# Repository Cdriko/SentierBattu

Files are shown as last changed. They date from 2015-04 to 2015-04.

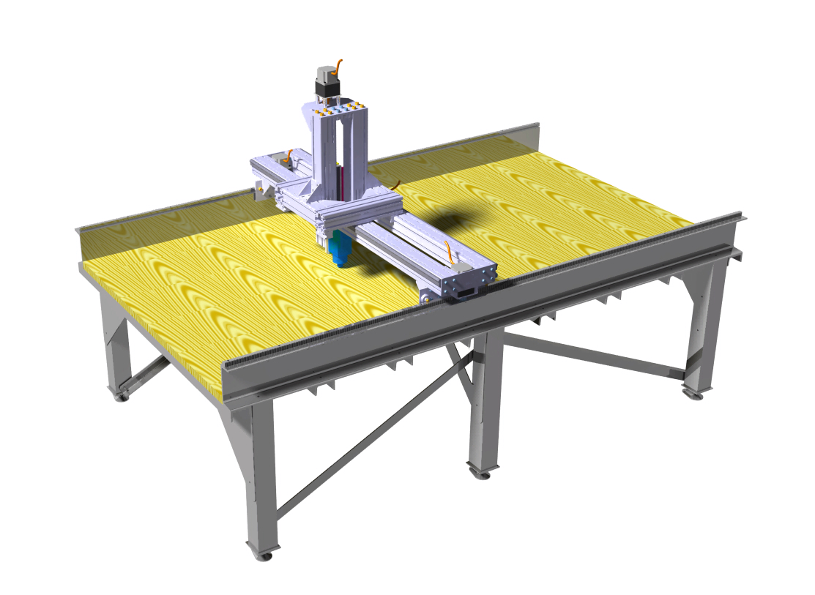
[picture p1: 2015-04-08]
sentierBattu.projet.jpg

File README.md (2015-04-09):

# SentierBattu
large CNC opensource router

Created by association PiNG 
http://pingbase.net

License : creative comons CC-BY-SA

Cedric Doutriaux

Laurent Malys

Philippe Bonet

Eric Chotard

Laurent Berthelot

with the help of

IUT of Nantes

more infos on
http://fablabo.net/wiki/SentierBattu

#######

For piloting it use fabmodules
https://github.com/FabModules/fabmodules-html5

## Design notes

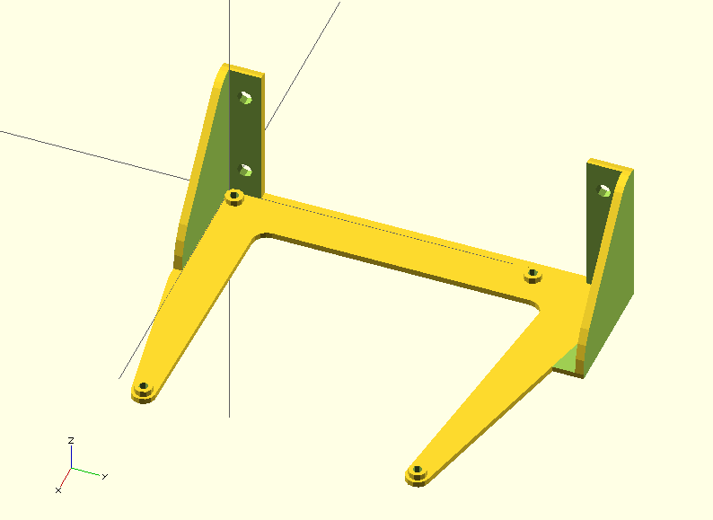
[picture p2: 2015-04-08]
electrics/electronics/smoothieBox/smoothifixation.png

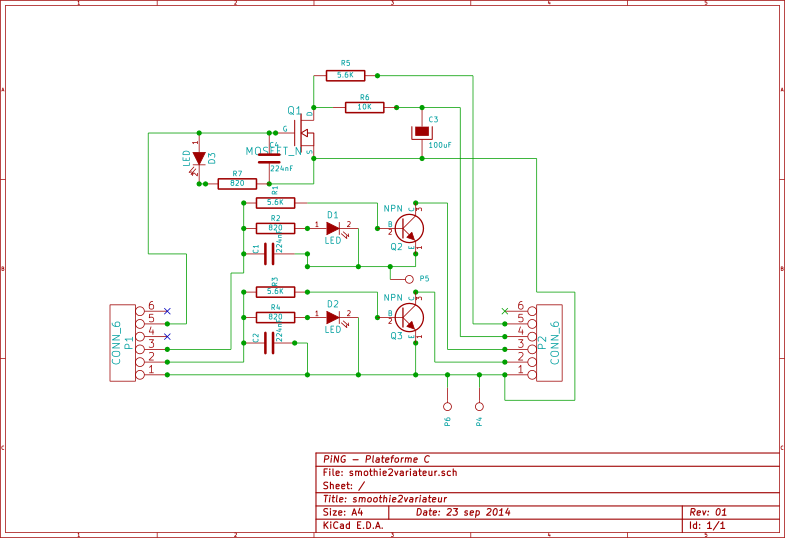
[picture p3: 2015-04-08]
electrics/electronics/Smothie2variateur.png

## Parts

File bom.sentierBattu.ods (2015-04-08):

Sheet: Résumé
Budget Machine CNC
electronique | 3792,45
mécanique | 5541,34312
Budget total machine | 9333,79312
Budget prévu | 9100

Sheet: electronique
electronique
 |  | qtte | fournisseur | modele | ref | option PP
controleur moteur |  | 3 | http://www.geckodrive.com/geckodrive-step-motor-drives/g201x.html |  |  | 120 | 360
moteur |  | 4 | http://www.orientalmotor.fr/Products/Stepper_motors/Stepper_motors/2phase_motors_pk/?arid=4646 | Motoreducteur nema34 | PK296AE-SG7.2 | 253,5 | 1014
Transformateur 220/24 |  | 1 |  |  |  | 170 | 170
 |  |  |  |  |  |  | 0
 |  | 1 |  |  |  | 0 | 0
moteur meche |  | 1 | www.fimec.it | 1.5KW 18/24000 RPM HF SPINDLE MOTOR | HM73d-060 | 585 | 707,85
controleur meche |  | 1 | www.fimec.it | INVERTER MONOFASE 220V | DSR2M022 | 360 | 435,6
 |  |  |  |  |  |  | 0
Armoire+rails |  | 1 |  |  |  | 120 | 120
cosses marqueurs |  | 1 |  |  |  | 50 | 50
Boutons |  | 5 |  |  |  | 5 | 25
arret d'urgence |  | 3 |  |  |  | 30 | 90
marche (poussoir) |  | 1 |  |  |  | 30 | 30
contacteur |  | 1 |  |  |  | 100 | 100
fins de course (logique + et -) |  | 6 |  |  |  | 40 | 240
ordinateur |  | 1 |  |  |  | 150 | 150
Cables / relais |  | 1 |  |  |  | 300 | 300
pour circuit electrique
disjoncteur diferentiel 30mA 20A | Q1 |  | rs | Disjoncteur iID 2pôles 25A 30mA c.a. | 510-6478
disjoncteur magnéto thermique D 4A | Q2 |  | rs |  | 772-1240
disjoncteur D 10A | Q3 |  |  |  | 769-4738
Disjoncteur courbe C 25A | Q4 |  |  |  | 769-4615
Contacteur bobine 24Vcc + 3 poles NO | K1 |  |  |  | 394-9762
deux contacts BLOC CONT 2F FRONTAL | K1 |  |  |  | 394-9914
Filtre RFI MX2 200Vca 24A jusqu'à 2,2kW pour variateur | RFI |  |  |  | 705-1787
arrets d'urgence | AU1-2-3 | 3 |  |  | 330-8559
bouton poussoir démarrage | BP1 |  |  |  | 690-6884
pince à sertir |  |  |  |  | 247-391
blindage pour cables
cable de commande
marqueurs pour cables
Armoire+rails
 |  |  |  |  |  | TOTAL | 3792,45

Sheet: mécanique
Mécanique |  |  |  |  |  |  | fournisseurs
 | usage |  |  |  |  |  | FIO | HPC | AMD | radiospares
table
UPN 200X75X6m | rails longitudinaux | 6 | m |  |  | AMD Ouest chailloux (nantes) |  |  | 181,792
UPN 100X50X18m | structure transversale | 18 | m |  |  |  |  |  | 203,32
Profilé carré creux 100X100 4mm | pieds | 6 | m |  |  |  |  |  | 83,72
profilé en L 50X50 4mm | Contre-ventement | 6 | m |  |  |  |  |  | 47,84
plaque 4mm 2X1m | équerres | 2 | m² |  |  |  |  |  | 143,52
pieds réglabes | pieds | 6 | u |  | 300Kg gros patin |  | 62,28
guidages
scheaffler 3mX2 | guidage X | 6 | m |  | peut être moins cher en morceaux de 1m chez rs |  |  | 1100,32
chariots X4 | X | 4 | u | hepco W3X |  |  |  |  |  | 225,51776
douilles de guidage |  |  |  |  |  |  |  |  |  | X
 |  |  |  |  |  |  |  |  |  | X
clinquant (feuilles de callage) 1/10 & 5/100 | réglage surface guidages X
guidages bosh LF12S | Z | 0,5 | m |  | rail double | FIO st herblain (sautron) | 52,31
guidages bosh LF12C | Y | 1,75 | m |  | de rail double | aller sur place
charriots LF12 | Y Z | 8 | u |  | + lardons |  | 699,12
entraînements
Crémaillères 4X2 module 2 | X | 6 | m |  | Dents droites percées acier | HPC distributeur |  | 297,99536
Pignons module 2 | X et Y | 4 | u |  | ~ d 30mm |  |  |  |  | X
crémaillère bosh module 2 | Y | 1,75 | m
vis a bille (500mm) diametre 16 pas~ 5mm | Z | 1 | u |  |  |  |  | 93,39564
ecrou pour vis a bille |  | 1 | u |  |  |  |  | 221,88192
palier fixe pour vis à bille |  | 1 | u |  |  |  |  | 302,5282
profilé 'bosh' 90X90mmn 4 trous | Chassis Y Z | 6 | m |  |  |  | 395,08
equerres bosh |  | 20 | u |  |  |  | 285,4
lardons bosh / equerres + guidages +charriots |  | 50 | u |  |  |  | 37
 |  |  |  |  |  |  |  |  |  |  | 0
 |  |  |  |  |  |  | 2289,32 | 2016,12112 | 660,192 | 575,71
 |  |  |  |  |  |  | 5541,34312

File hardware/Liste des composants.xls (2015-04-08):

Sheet: Feuil1
Quantité | Référence
3 | sg_2020-2000x
2 | poutrelle_upn_200_x_1_75
2 | rail
2 | 3842992415_104211921
2 | BOUCHON
20 | Vis chc m12 x 40
20 | Rondell m12
4 | Galet guidage axe x
8 | Ecrou_M12
4 | l1-16101
4 | Axe roulement
4 | Rondelle d'appui D19
4 | Vis M8 x 12
2 | TOLE GUIDAGE
4 | Equerre 90x90xx
40 | Vis_M8x25
56 | rondelle_9
101 | Ecrou BOSCH M8
74 | Lardon tige BOSCH-M8X25
2 | Tole moteur
4 | PK296AE-SG7.2
8 | Vis_M6x20
8 | rondelle_6-6
24 | vis_M8x16
3 | Pignon_moteur
2 | Profile de serrage LF12C x 750
2 | Tige de guidage LF12 x 750
8 | vis_M8x30
4 | plaque support fin de course
4 | Fin_de_course_DL
8 | vis_07175-04x25
8 | ecrou_M4
1 | UPN 200x75x3000
8 | UPN 100x50x1750
1 | UPN 200x75x3000.1
1 | Plaque martyr
4 | equerre.1
2 | equerre
6 | PLAT PIED
18 | ecrou_3300-408
6 | tige filetée M12
6 | bosch_3842538680_38kq0hejlxcjebzu4812w7e6w
6 | Tube carré 100x100x820
6 | Part8
8 | vis_m10_20
2 | contreventement long
2 | contreventement court
2 | sg_20-20-3000
2 | railx3000
36 | ISO 7089 WASHER 12x24 STEEL GRADE A PLAIN NORMAL SERIES
5 | Butée axe X
1 | Planche bois
2 | Profil 90*90 X
2 | profil 90*90 Y
8 | chariot Y
8 | Equerre 90*90
1 | IPN
2 | Plaque_machine_chariot_Y
2 | vis_07175-06x12
20 | ISO 4762 SCREW M12x30 STEEL HEXAGON SOCKET HEAD CAP
2 | 500
1 | 3842992415_102757468
1 | Profile de guidage LF12S
1 | 3842993062_10302278
2 | 3842993968_103214500
1 | 3842990335_103324390
1 | 3842992415_104211921_2
1 | Plaque broche
1 | broche
1 | Part2
1 | Ecrou_GBS-F-1605
4 | tube
4 | ISO 10642 SCREW M6x10 STEEL HEXAGON SOCKET COUNTERSUNK HEAD
2 | ISO 10642 SCREW M6x30 STEEL HEXAGON SOCKET COUNTERSUNK HEAD
2 | ISO 4762 SCREW M8x40 STEEL HEXAGON SOCKET HEAD CAP
2 | lardon_M8
6 | ISO 4032 NUT M5 STEEL GRADE A HEXAGON
6 | ISO 10642 SCREW M5x25 STEEL HEXAGON SOCKET COUNTERSUNK HEAD
2 | lardon M6
1 | accouplement
1 | Vis_KGS-1605-1000TR7
1 | Part1
2 | cale 6mm
1 | Palier_RPB12
1 | Support_palier
4 | Entretoise_moteur
1 | Rehausse_moteur
1 | tranche profilé 90x90x20
1 | Part3
4 | ISO 4762 SCREW M5x35 STEEL HEXAGON SOCKET HEAD CAP
8 | ISO 4762 SCREW M8x30 STEEL HEXAGON SOCKET HEAD CAP
1 | boitier_electrique
3 | Boutan_arret_urgence
1 | AL-AL001-1 1/2in

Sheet: Feuil2
Quantité | Référence |  | commentaire
3 | sg_2020-2000x | ok
2 | poutrelle_upn_200_x_1_75
2 | rail
2 | 3842992415_104211921
2 | BOUCHON | ok
4 | l1-16101
4 | Axe roulement | ok
2 | TOLE GUIDAGE | ok
4 | Equerre 90x90xx
2 | Tole moteur | ok
4 | PK296AE-SG7.2
8 | rondelle_6-6
3 | Pignon_moteur
2 | Profile de serrage LF12C x 750
2 | Tige de guidage LF12 x 750
4 | plaque support fin de course | ok | poutre z -9
4 | Fin_de_course_DL
1 | UPN 200x75x3000
8 | UPN 100x50x1750
1 | UPN 200x75x3000.1
1 | Plaque martyr
4 | equerre.1
2 | equerre
6 | PLAT PIED
18 | ecrou_3300-408
6 | bosch_3842538680_38kq0hejlxcjebzu4812w7e6w
6 | Tube carré 100x100x820
6 | Part8
2 | contreventement long
2 | contreventement court
2 | sg_20-20-3000
2 | railx3000 | ok | ( rail guidage x )
36 | ISO 7089 WASHER 12x24 STEEL GRADE A PLAIN NORMAL SERIES
5 | Butée axe X
1 | Planche bois
2 | Profil 90*90 X
2 | profil 90*90 Y
8 | chariot Y
8 | Equerre 90*90
1 | IPN | ok
2 | Plaque_machine_chariot_Y
1 | 3842992415_102757468
1 | Profile de guidage LF12S
1 | 3842993062_10302278
2 | 3842993968_103214500
1 | 3842990335_103324390
1 | 3842992415_104211921_2
1 | Plaque broche
1 | broche
1 | Part2
4 | tube
1 | Part1
2 | cale 6mm
1 | Palier_RPB12
1 | Support_palier
4 | Entretoise_moteur | ok
1 | Rehausse_moteur | ok
1 | tranche profilé 90x90x20
1 | Part3
1 | AL-AL001-1 1/2in
 | Plans fais mon pas de correspondance en nomenclature ????
 | poutre z 1 | ok
 | poutre z 2 | ok
 | poutre z 4 | ok
 | vis kgs | ok
 | poutre z 6 | ok
 | poutre z 7 | ok
 | profilés | ok
 |  | ok
 |  | ok
 |  | ok
 |  | ok
 |  | ok

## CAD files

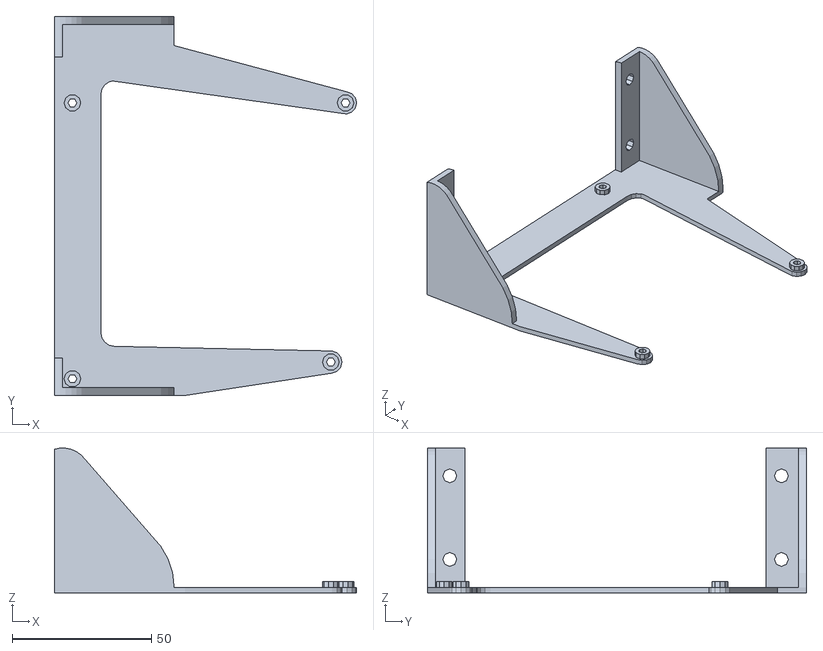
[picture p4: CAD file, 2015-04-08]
electrics/electronics/smoothieBox/SmootieBox.stl
108.5 x 136.0 x 51.9

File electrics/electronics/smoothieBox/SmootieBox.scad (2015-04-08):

/*
Smoothieboard attach for electrical enclosure
*/



module smoothieholes(){
translate([0,0,-4])
union(){//holes
		
			translate([3.5,3,-30])
			cylinder(r=1.6,h=60);
			
			translate([3.5,102,-30])
			cylinder(r=1.6,h=60);
			
			translate([(105-8.77),9,-30])
			cylinder(r=1.6,h=60);
			translate([(105-3.5),102,-30])
			cylinder(r=1.6,h=60);
		
		}


}



module SmoothiePlate(){
	//-------------------smoothieBoard
	difference(){
translate([0,0,-0.75])
		cube([105,130,1.5]);
		translate([0,0,-1])
		smoothieholes();
	}
//USB port
translate([77,0,-0.75])
		cube([12.3,16.6,10.8]);
}

//background rail
module backSupport(){
	//back support
translate([0,0,-0.5])
linear_extrude(height = 1,center=true){
union(){
	hull() {
	   translate([3.5,3,0])
				circle(12);
	   translate([(105-8.77),9,0]) circle(4);
	}
	hull() {
	translate([(105-3.5),102,0])circle(4);
	 translate([3.5,122,0])
				circle(10);
	translate([3.5,127,0])
				circle(4);
	 }
	difference(){
		hull() {
		translate([(3.5),102,0])circle(17.2);
		 translate([(3.5),9,0]) circle(15);
		 }
		hull() {
		translate([(18.7),105,0])circle(5);
		 translate([(18.7),19.6,0]) circle(5);
		 }
	}
}
}

union(){//holes
		
			translate([3.5,3,0])
			cylinder(r=3,h=1);
			
			translate([3.5,102,0])
			cylinder(r=3,h=1);
			
			translate([(105-8.77),9,0])
			cylinder(r=3,h=1);
			translate([(105-3.5),102,0])
			cylinder(r=3,h=1);
		
		}



}



module arch(){//for the wall fixation

	difference(){
	
		//Arch
		rotate([90,0,0])
		linear_extrude(height = 15,center=true)
		hull() {
				translate([22,0,0])circle(25);
				 translate([7,40,0]) circle(10);
				 }
		union(){//wall holes

rotate([0,-90,0]){
			translate([10,2,-40])
			cylinder(r=2.5,h=60);
			translate([40,2,-40])
			cylinder(r=2.5,h=60);
}

		}
		
	
	}
}


difference(){





	union(){

difference(){
translate([-7,0,0])
union(){
		//archs
		translate([0,3,0])
		arch();




		translate([0,126,0])
mirror([0,1,0])
		arch();
}

union(){
translate([0,-0.2,0])
cube([105,130.4,500]);

}
}
		
		
		//total backplate
		difference(){
		scale([1,1,2])
		backSupport();
		
		}
	}

	union(){//bounding box
	
		translate([-10,133,-20])
		cube([105,130,300]);
		translate([-10,-33,-20])
		cube([105,30,300]);
		
		translate([-3,137.5,-20])
		rotate([0,0,180])
		cube([105,160,300]);
		
		translate([-20,-25,-32])
		cube([305,300,30]);
smoothieholes();
	
	}

}
///smoothie preview
//color([0.9,0.4,0.2,0.5])
//SmoothiePlate();

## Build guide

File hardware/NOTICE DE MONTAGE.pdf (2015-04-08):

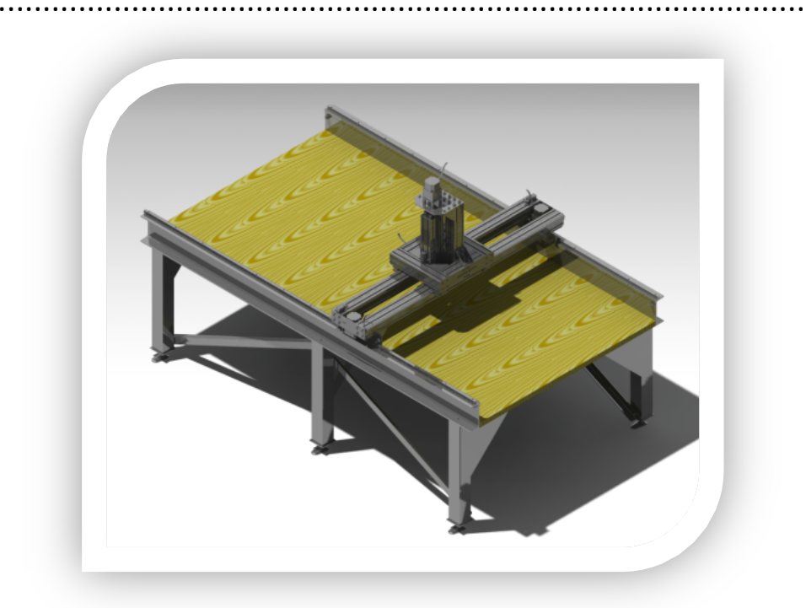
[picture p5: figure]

FAB

LAB

– Workshop

CNC

Router 1

# NOTICE

DE

# MONTAGE :

SOMMAIRE :

Description

des

sous

Montage

du

Assemblage

des

traverses

Mise

en

place

des

pieds

et

des

positionnement

des

Retournement

du

Montage

du

chariot

Assemblage

de

la

structure

axe

Assemblage

des

deux

ensembles

de

Assemblage

des

deux

parties

Montage

de

Montage

du

chariot

Matériels

Montage

du

chariot

AXE

Z

Structure

AXE

DESCRIPTION

DES

SOUS ENSEMBLES :

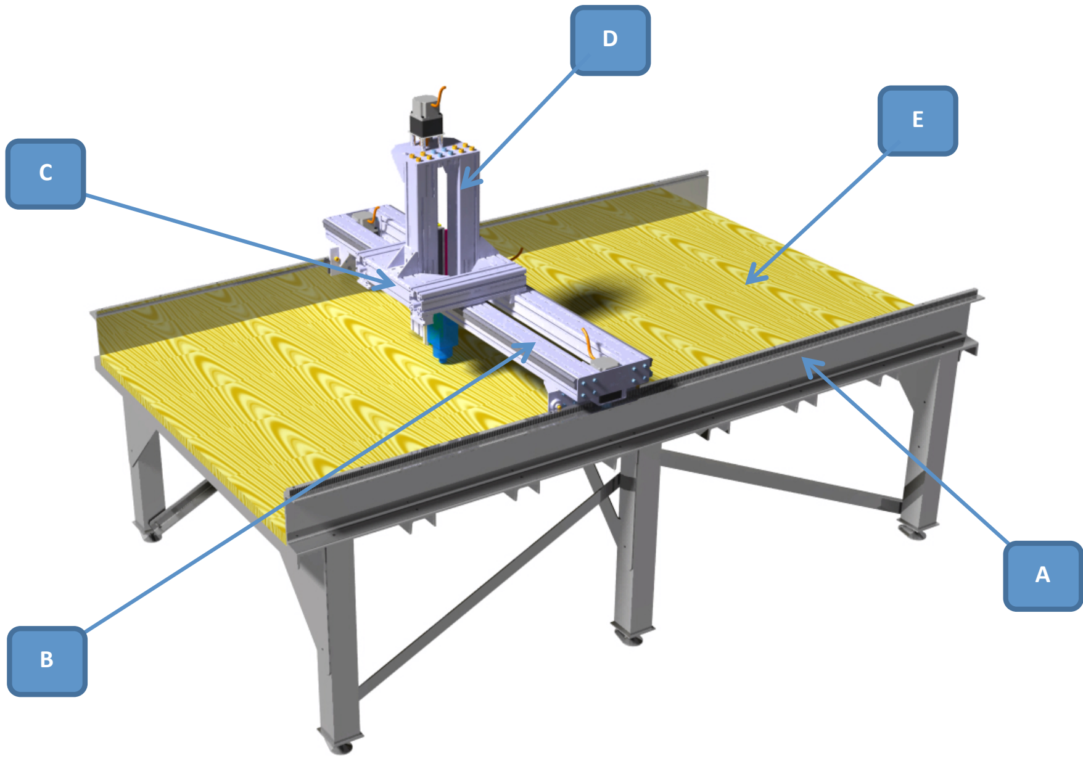
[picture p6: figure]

### A. La

### machine

### est

### composée

### d’un

bâti,

### sur

### lequel

### sont

### fixées

### les

### crémaillères

de

### l’axe

x

### ainsi

### que

### les

### deux

### rails

de

guidage.

### B. Le

### chariot

X

### est

### guidé

### sur

### les

### deux

### rails

### par

### des

galets,

la

### transmission

de

### mouvement est

### assurée

### par

### deux

### moteurs

### électriques

### montés

en

### vis

à

vis.

### C. Le

### chariot

Y

### est

### guidé

### sur

le

### chariot

de

### l’axe

X,

la

### transmission

### est

### assurée

### par

un

### moteur

### électrique

### engrenée

### sur

### une

crémaillère.

### D. L’axe

Z

### est

### porté

### par

le

### chariot

Y,

### cet

### axe

### porte

la

broche.

La

### transmission

### est

### assurée par

### une

### vis à

bille.

### E. Le

### plateau

### support

### autrement

### appelé

### plaque

### martyr

### est

### réalisé

en

### contreplaqué

de
40

mm.

MONTAGE

DU

BATI :

ASSEMBLAGE

DES

TRAVERSES

(UPN) :

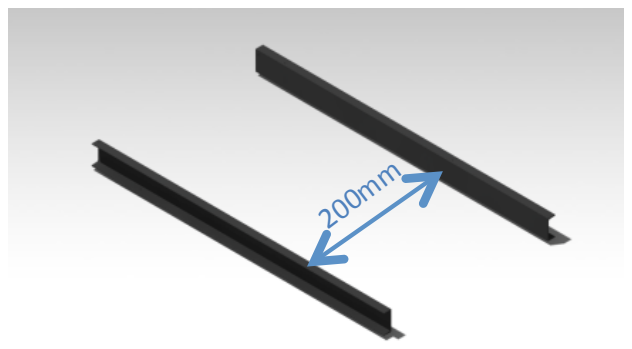
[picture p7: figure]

- Dans

un

premier

temps,

positionner

les

deux

grosses

traverses
(UPN

200x75x3000) au

sol

sur

des

cales,

dégauchir

l’ensemble.
Puis,

positionner

et

dégauchir

les

traverses

extrêmes

après

avoir
serré

légèrement.

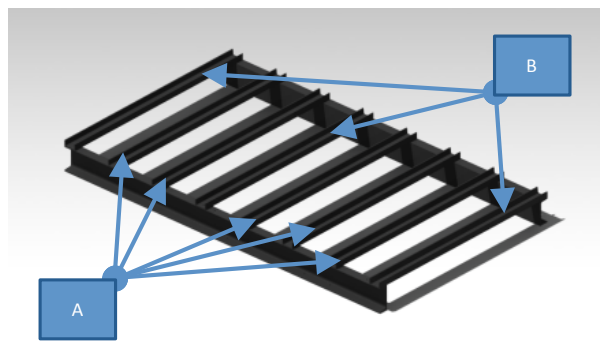
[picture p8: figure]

- Pour

le

déchauchissage,

utiliser

des

équerres,

un

mètre

afin

de
mesurer

la

largeur

et

les

diagonales.

- Positionner

et serrer

les

autres

traverses (UPN

100x50x1750). Il

y

a
deux

types

de

traverses.

Trois

d’entre

elles

(Type

B)

possèdent

des
perçages

sur

les

flancs

de

l’UPN

pour

la

fixation

des

goussets

de
pieds.

MISE

EN

PLACE

DES

PIEDS

ET

DES

GOUSSETS :

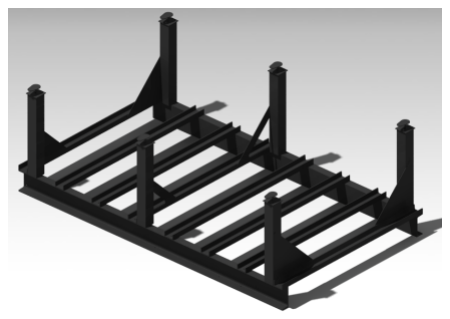
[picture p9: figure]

- Visser

les

pieds

dans

la

structure

sans

les

serrer à

l’aide

des

vis
M12,

positionner

les

goussets et

les

serrer

après

avoir

contrôler
les

équerrages

et

les

cotes

,

attention

,

les

deux

goussets

centraux
sont

différents

de

ceux

des

extrémités.

POSITIONNEMENT

DES

CONTREVENTEMENTS :

- Dans

cette

étape,

il

va

falloir

souder

les

têtes

de

vis

(En

rouge)

sur
la

face

intérieure

des

pieds.

Au

préalable,

il

faut

visser

les

vis

sur

le
contreventement

en

ayant

pris

soin

de

mettre

un

contre

écrou
coté

tête

de

vis

afin

de

dégager

celle-‐ci

pour

le

pointage.

RETOURNEMENT

DU

CHASSIS :

- Pour

retourner

le

châssis,

positionner

deux

sangles

autour

d’un

des

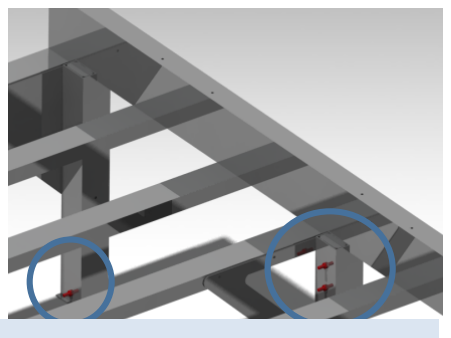
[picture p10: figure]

UPN

de

200

mm,

positionner

deux
tasseaux

qui

supporteront

l’UPN

opposé

lors

de

la

phase

de

rotation.
- Une

fois

l’ensemble

retourné,

lever

l’ensemble

à

la

verticale

à

une

vingtaine

de

centimètre

pour
pouvoir

monté

les

pieds

réglables

à

rotule.

On

peut

ensuite

repositionner

la machine

dans

sa

position
définitive

de

montage.
- Il

faut

ensuite

dégauchir l’ensemble,

à

l’aide

d’un

laser,

de

règles

ou

de

niveaux

de

précision.

La
largeur

des

deux

UPN

de

200

mm

doit

également

être

réglée,

prise

de

côtes

et

de

diagonales.

MONTAGE

DU

CHARIOT

X :

ASSEMBLAGE

DE

LA

STRUCTURE

AXE

X :

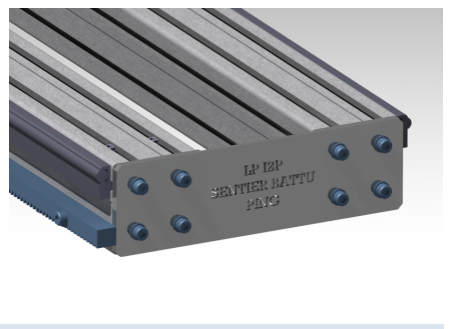
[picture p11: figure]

- Positionner

les

deux

profilés

de

90x90

et

fixer,

de

chaque

côté,

la
tôle

de

4mm

à

l’aide

des

8

vis

M12.

Il

faut

que

l’écart

entre

les
deux

profilés

soit

de

120mm

en

cote

intérieure.
- On

peut

ensuite

positionner

les

deux

rails

de

guidage

Bosch

sur

les
profilés

en

les

clipsant

dans

les

rainures.

Vissage

de

la

crémaillère
à

l’aide

de

lardons

de

profilés.

ASSEMBLAGE

DES

DEUX

ENSEMBLES

DE

GUIDAGE :

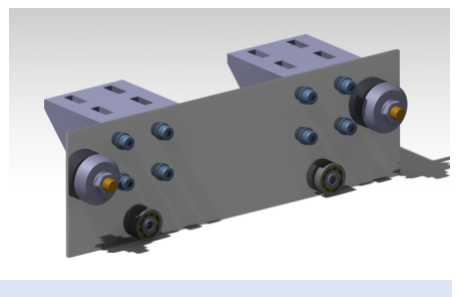
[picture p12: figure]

- Fixer

les

deux

équerres

Bosch

sur

la

tôle

support
- Positionner

les

deux

galets

et

les

deux

roulements

ASSEMBLAGE

DES

DEUX

PARTIES

MOTEURS :

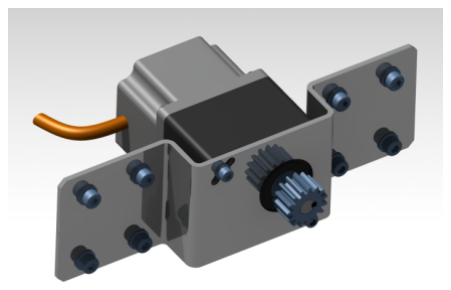
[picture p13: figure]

- Positionner

le

moteur

dans

son

logement

et

le

fixer

à

l’aide

des
deux

vis.
- Monter

le

pignon

sur

l’arbre

moteur

à

l’aide

de

la

clavette

et

le
maintenir

en

position

avec

la

vis

sans

tête

qui

appuie

sur

le
méplat

de

l’arbre.

MONTAGE

DE

L’ENSEMBLE :

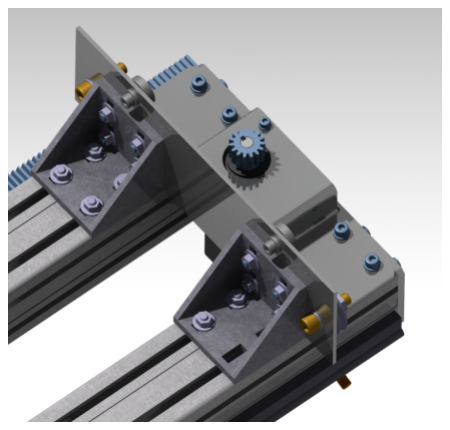
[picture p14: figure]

- Fixer

les

deux

ensembles

de

guidage

avec

les

écrous

et

lardons
pour

profilés.
- Fixer

les

deux

parties

moteurs

à

l’aide

des

8

vis.

MONTAGE

DU

CHARIOT

Y :

MATERIELS

NECESSAIRES :

Afin

de

réaliser

le

montage

du

chariot

vous

aurez
besoin

de :

-‐ 2 profilés

Bosch

de

90*90

de

450mm

de
| long
-‐ | 2 profilés

Bosch

de

90*90

de

310mm

de
| long
-‐ | 4 équerres

Bosch

de

90*90
-‐ 4 chariots

de

guidage

linéaire

LF12C
-‐ 34

lardons

males

M8

Bosch
-‐ 34

écrous

à

embase

M8
-‐ 10

lardons

femelles

M8

Bosch
-‐ 1 équerre

poutre

I

usinée
-‐ 2 vis

FHC

M8*12

-‐ 4 vis

CHC

M6*10
-‐ 4 rondelles

M6
-‐ 1 crémaillère

(Z=15)
-‐ 1 moteur

PK296AE
-‐ 2 plaques

gravées
-‐ 16

vis

CHC

M12

Et

du | matériel

suivant :

-‐ | 1 serre-‐joint
-‐ | 1 clef

à

pipe

et

une

clé

plate

de

13

pour
| les

écrous

à

embase
-‐ 1 clef

Allen

de

5

pour

les

CHC
-‐ 1 clef

Allen

de

…

pour

les

FHC

MONTAGE :

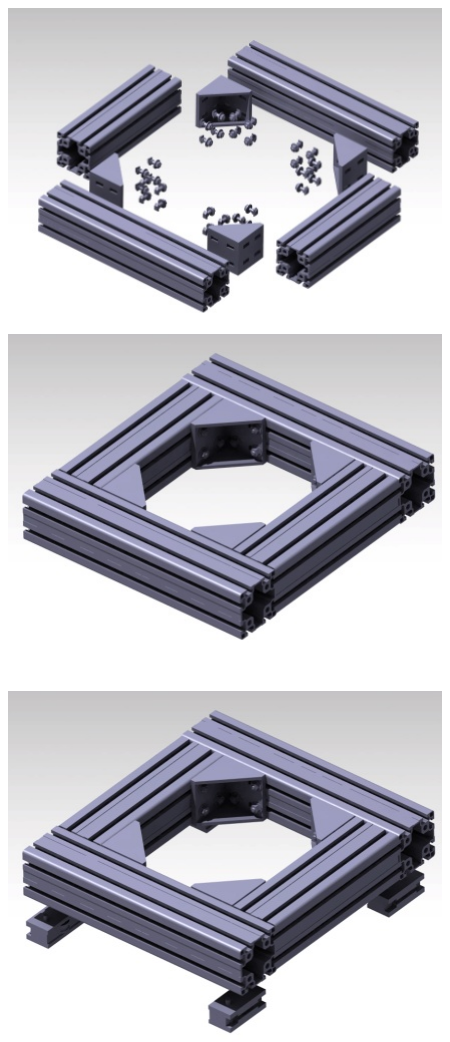
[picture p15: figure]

- Dans

un

premier

temps

vous

assemblerez

les

4

profilés

ensembles
à

l’aide

des

4

équerres

comme

ci-‐dessous

avec

32

des

lardons
males

et

32

des

écrous

à

embase

en

serrant

à

la

main

afin

de
permettre

le

glissement

des

différents

profilés
- Afin

de

réaliser

le

bon

écart

entre

les

deux

profilés

de

310

vous
aurez

besoin

de

3

profilés

de

90*90

de

petite

longueur

afin

de

les
utiliser

comme

cales

que

vous

serrerez

entre

les

profilés

pour
ensuite

serrer

les

32

écrous.
- Vous

placerez

ensuite

les

4

chariots

de

guidage

sur

les

profilés

de
450mm

de

long

à

l’aide

des

8

lardons

femelles

que

l’on

serra

à

la
main

si

possible

puis

à

la

clef

Allen

sans

forcer

afin

de laisser

la
possibilité

de

positionné

les

guidages

sur

les

rails

du

chariot

X.
- Il

faudra

ensuite

placer

le

chariot

Y

sur

le

chariot

X

afin

de

régler
les

guidages

et

de

préparer

la

poutre

en

I

et

le

moteur.
- Comme

cité

précédemment

vous

réglerez

les

guidages

à

l’aide

des
excentriques

sur

les

deux

rails

du

chariot

Y.
- Ensuite

vous

placerez

le

moteur

sur

l’équerre

avec

un
positionnement

médian

par

rapport

aux

trous

oblong

que

vous
serrerez

à

l’aide

de

2

vis

M6

et

2

rondelles.

- Après

ce

premier

réglage

placé

l’équerre

sur

le

bord

du

chariot

Y
placé

sur

le

chariot

X

du

côté

de

la

crémaillère

et

estimez

le

jeu
qu’il

y

a

entre

le

pignon

et

la

crémaillère

et

la

poutre

afin

de
rapprocher

ou

d’éloigner

le

moteur

ou

de

le

rapprocher

de

la
crémaillère.
- Recommencez donc

cette

étape

autant

de

fois

qu’il

sera

nécessaire
et

une

fois

que

l’équerre

sera

à

plat

et

le

pignon

bien

placé,

vous
pourrez

ajouter

les

deux

autres

vis

afin

de

fixer

le

moteur

sur

l’équerre.
- Retirez

le

chariot

Y

du

chariot

X

afin

de

pouvoir

fixer

l’équerre

sur
le

chariot

Y.
- Fixé

l’équerre

sur

la

poutre

à

l’aide

des

2

vis

FHC

et

des

lardons
femelles

du

côté

intérieur

et

les

2

lardons

males

et

écrous

à
embase

restants,

essayez

de

placer

l’équerre

entre

les

deux
chariots

de

guidage

afin

de

placer

la

motorisation

le

plus

au

centre

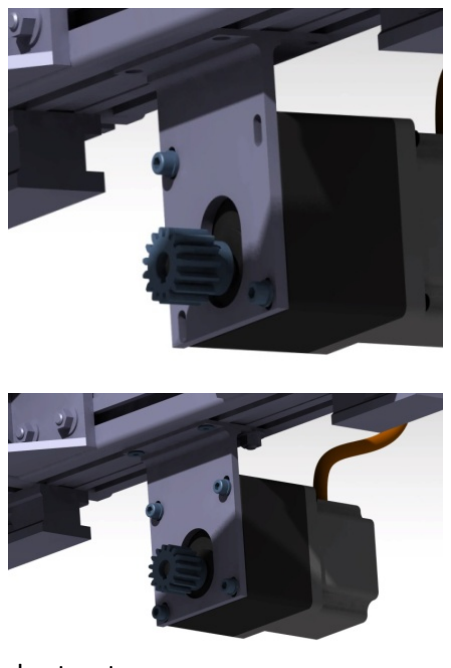
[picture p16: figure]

de

la

structure.
- Vous

placerez

enfin

les

deux

plaques

gravés

à

l’aide

des

16

vis

CHC

sur

les

extrémités

des

profilés
taraudé.

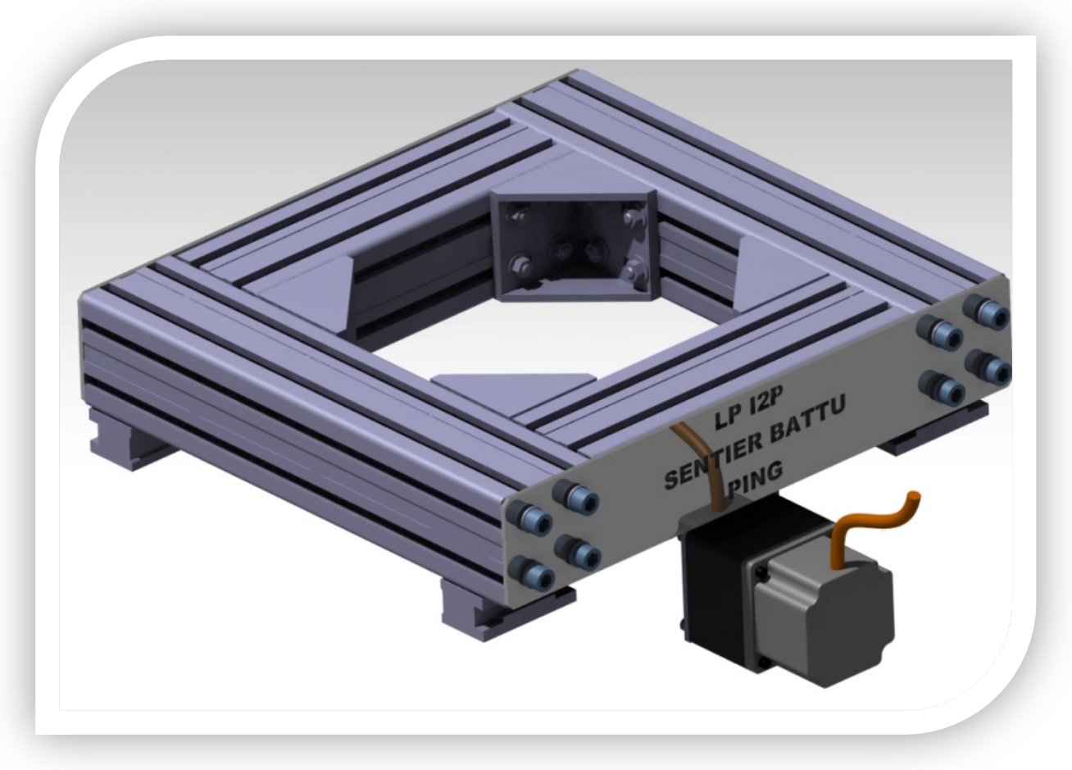
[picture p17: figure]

MONTAGE

DU

CHARIOT

Z :

AXE

Z

MOBILE :

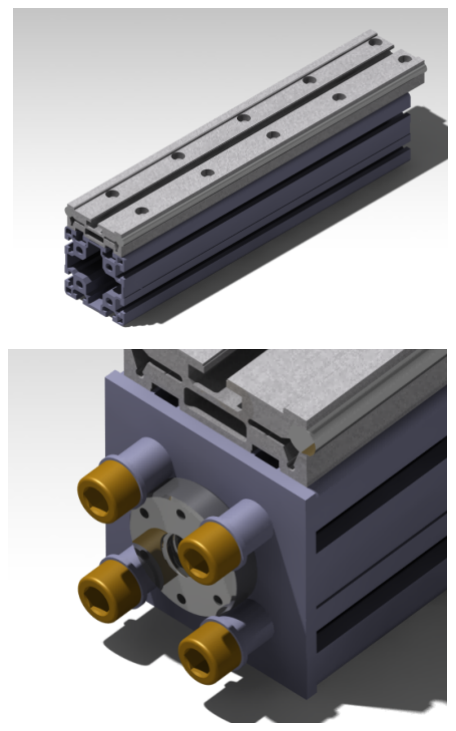
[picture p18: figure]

- Montage

du

profilé

de

guidage

sur

le

profilé

Bosch

de

90x90

et
mise

en

place

des

deux

axes

de

guidage

fournit

avec

le

profilé

de
guidage.
- Mise

en

place

de

l’écrou

de

vis

à

billes

sur

sa

plaque

en

acier

de
4mm

avec

6

vis

FHC

M5x25

et

6

écrou

H

M5.

- Mise

en

place

des

4

vis

M12

pour

fixer

la

plaque

support

de
l’écrou

sur

le

profilé.

Quatre

entretoises

ou

tubes

sont
nécessaires

car

les

têtes

de

vis

CHC

entraient

en

collision

avec
l’écrou

de

vis

à

billes.

- Mettre

les

deux

vis

FHC

M8

situé

sur

le

bas

de

la

plaque

puis

fixer
la

broche

sur

la

plaque

de

4mm

qui

permet

de

maintenir

la
broche

sur

le

guidage

Bosch.

On

utilise

4

vis

FHC

M6x12max.

On
visse

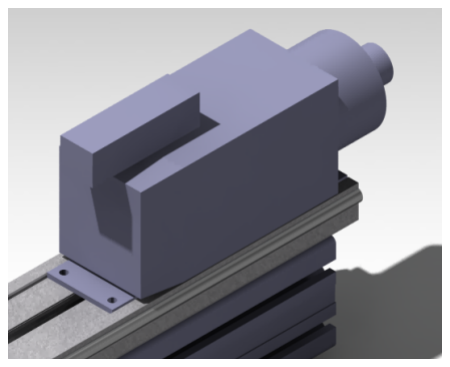
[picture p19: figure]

ensuite

les

deux

vis

inférieures

qui

ont

été

positionné

au
préalable

puis

les

deux

vis

CHC

M8.

Cette

plaque

est

fixée

à

l’aide
des

4

passages

de

vis

du

profilé

de

guidage

Bosch.

- Enfin

on

peut

positionner

le

capteur

de

fin

de

course

sur

le

profilé
Bosch

de

90x90.

La

hauteur

du

capteur

est

à

régler

et

à

définir
selon

l’épaisseur

de

la

plaque

martyre.

•

STRUCTURE

AXE

Z :

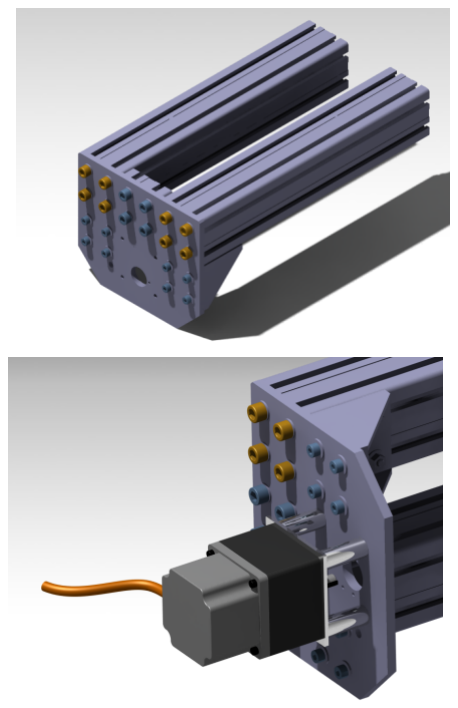
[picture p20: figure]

- Mettre

en

place

les

deux

profilés

de

500mm.

(Entraxe

intérieur
de

90mm.

- Positionner

la

tranche

de

profilé

de

90x90

qui

permet

d’assurer
l’entraxe

entre

les

deux

profilés. Cet

entraxe

est

important
puisque

la

broche

va

translater

entre

les

deux

profilés

Bosch.

- Positionner

la

plaque

aluminium

et

la visser

à

l’aide

des

8

vis
M12

sur

les

extrémités

des

deux

profilés.

- Visser

les

deux

équerres

à

l’aide

des

8

lardons

et

des

8

vis

M8

qui
permettront

de

renforcer

la

structure

Z.

Lors

du

montage

de

ces
équerres

il

faut

assurer

la

perpendicularité

de

la

plaque
aluminium

avec

les

deux

profilés

90x90

de

500mm.

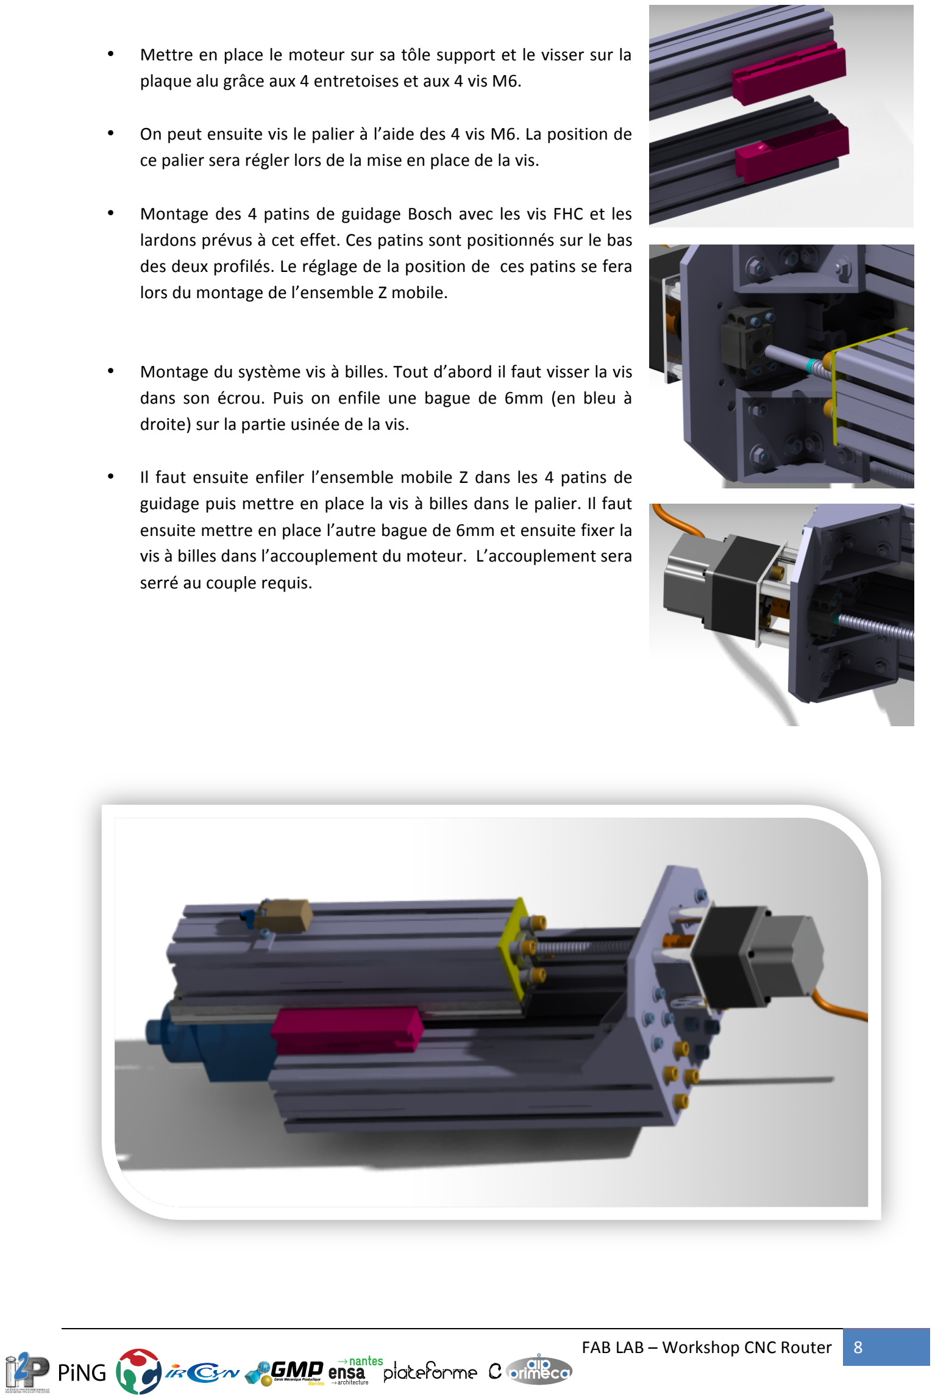
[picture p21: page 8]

- Mettre

en

place

le

moteur

sur

sa

tôle

support

et

le

visser

sur

la
plaque

alu

grâce

aux

4

entretoises

et

aux

4

vis

M6.

- On

peut

ensuite

vis

le

palier

à

l’aide

des

4

vis

M6.

La

position

de
ce

palier

sera régler

lors

de

la

mise

en

place

de

la

vis.

- Montage

des

4

patins

de

guidage

Bosch avec

les

vis

FHC

et

les
lardons

prévus

à

cet

effet.

Ces

patins

sont

positionnés

sur

le

bas
des

deux

profilés.

Le

réglage

de

la

position

de

ces

patins

se

fera
lors

du

montage

de

l’ensemble

Z

mobile.

- Montage

du

système

vis

à

billes.

Tout

d’abord

il

faut

visser

la

vis
dans

son

écrou.

Puis

on

enfile

une

bague

de

6mm

(en

bleu

à
droite)

sur

la

partie

usinée

de

la

vis.

- Il

faut

ensuite

enfiler

l’ensemble

mobile

Z

dans

les

4

patins

de
guidage

puis

mettre

en

place

la

vis

à

billes

dans

le

palier.

Il

faut
ensuite

mettre

en

place

l’autre

bague

de

6mm

et

ensuite

fixer

la
vis

à

billes

dans

l’accouplement

du

moteur.

L’accouplement

sera
serré

au

couple

requis.

ASSEMBLAGE

DES

DIFFERENTES

PARTIES :

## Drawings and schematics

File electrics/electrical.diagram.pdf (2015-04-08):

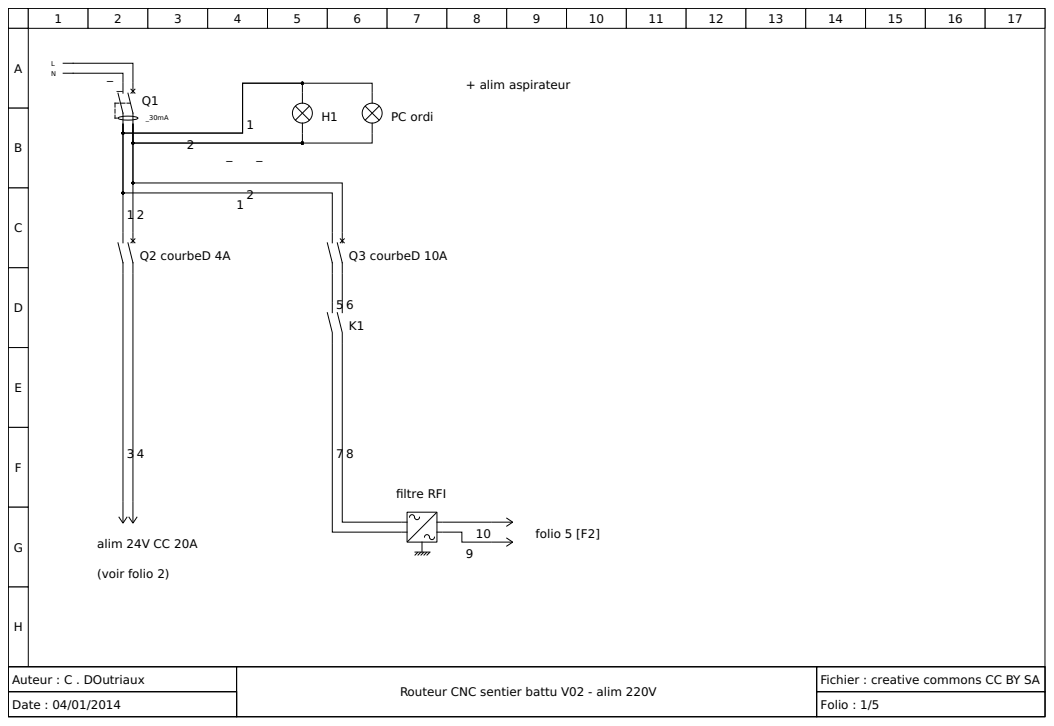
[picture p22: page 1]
Auteur : C . DOutriaux; Date : 04/01/2014; Folio : 1/5; PC ordi; Q2 courbeD 4A; Q3 courbeD 10A; + alim aspirateur; alim 24V CC 20A; (voir folio 2); filtre RFI; folio 5 [F2]

Fichier : creative commons CC BY SA

Routeur CNC sentier battu V02 - alim 220V

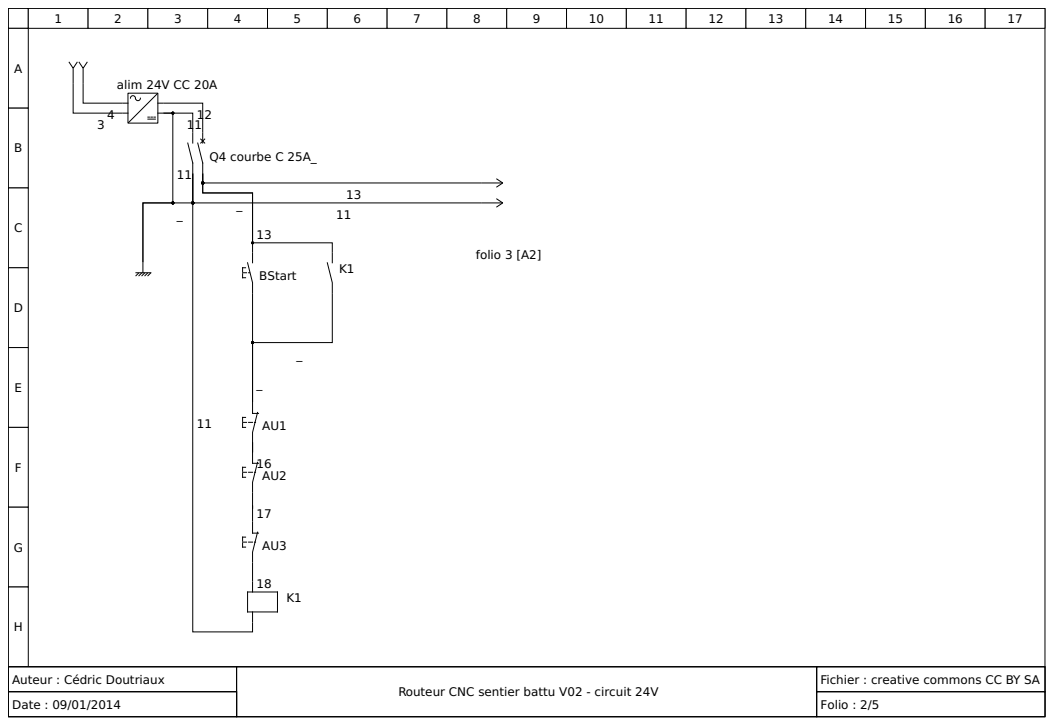
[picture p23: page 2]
Date : 09/01/2014; Folio : 2/5; Q4 courbe C 25A_; K1 BStart; alim 24V CC 20A; folio 3 [A2]

Auteur : Cédric Doutriaux

Fichier : creative commons CC BY SA

Routeur CNC sentier battu V02 - circuit 24V

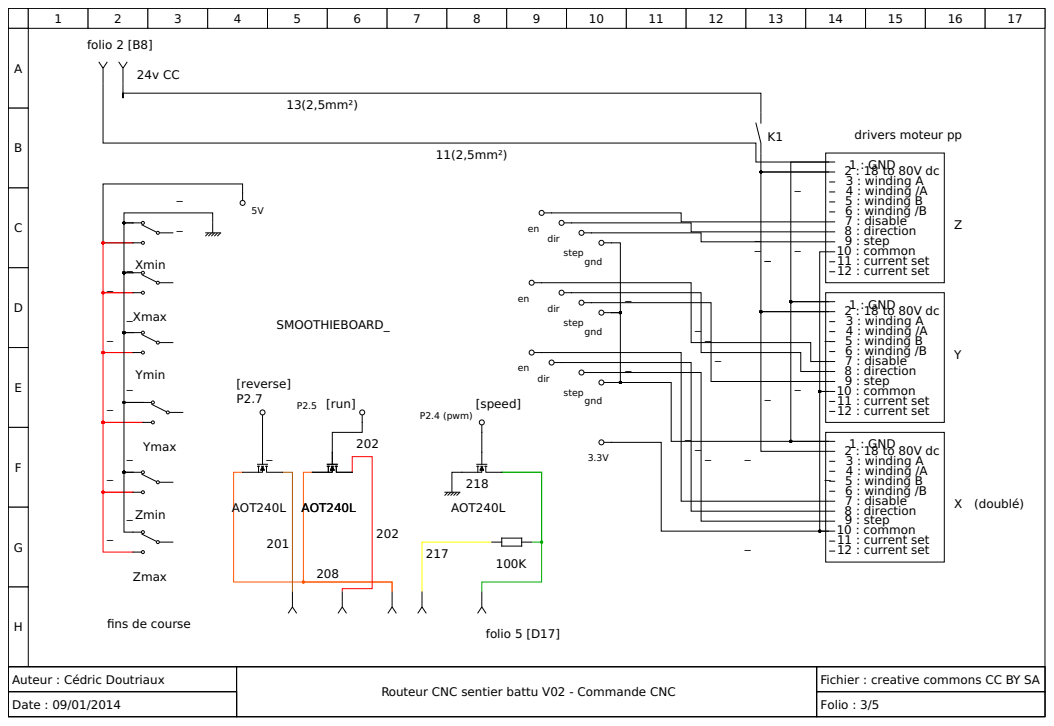
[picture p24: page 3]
11(2,5mm²); 13(2,5mm²); AOT240L; step; dir; gnd; 12 : current set; 11 : current set; 10 : common; 9 : step; 8 : direction; 7 : disable; 6 : winding /B; 5 : winding B; 4 : winding /A; 3 : winding A; 1 : GND; Xmax; Ymin; Ymax; Zmax; Zmin; Xmin; P2.4 (pwm); SMOOTHIEBOARD_; X (doublé); folio 2 [B8]; folio 5 [D17]; [run]; [speed]; [reverse] P2.7

drivers moteur pp

fins de course

Auteur : Cédric Doutriaux

Fichier : creative commons CC BY SA

Routeur CNC sentier battu V02 - Commande CNC

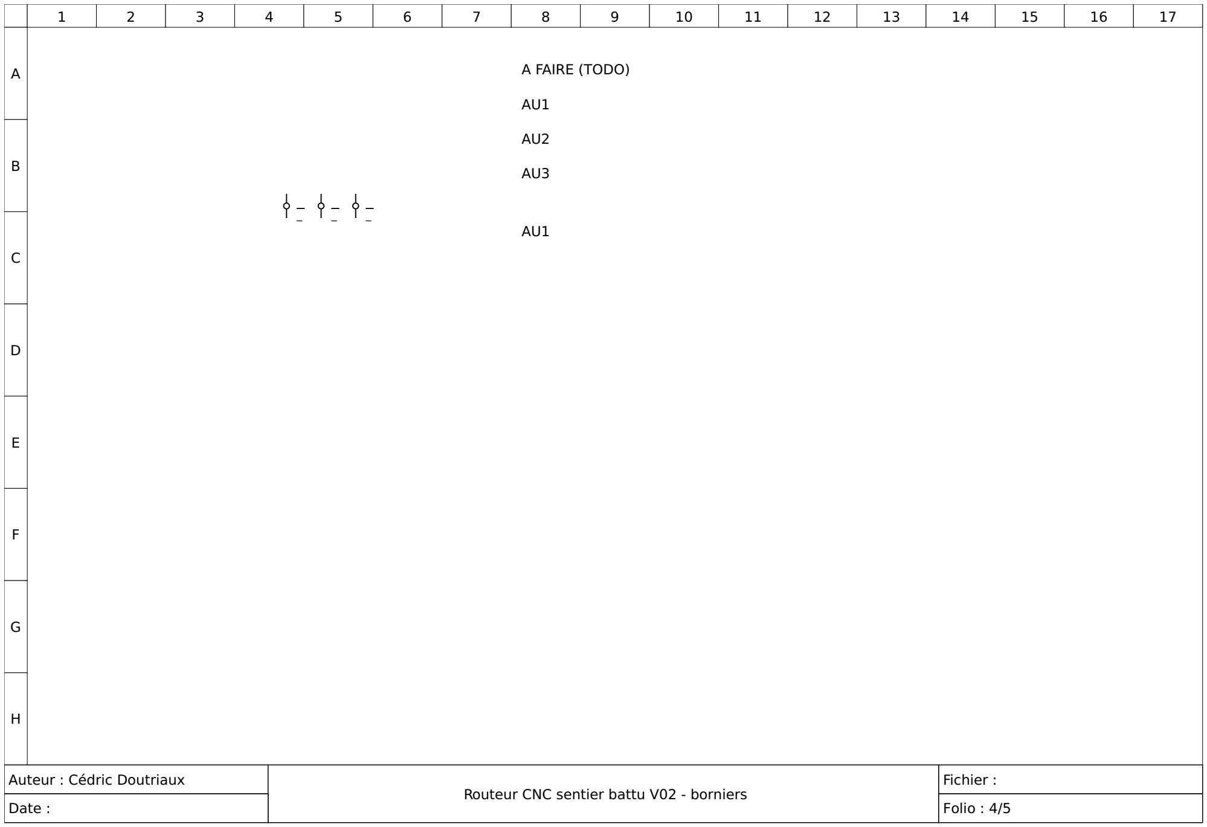
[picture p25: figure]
Date :; Folio : 4/5; A FAIRE (TODO)

Auteur : Cédric Doutriaux | Routeur CNC sentier battu V02 - borniers | Fichier :

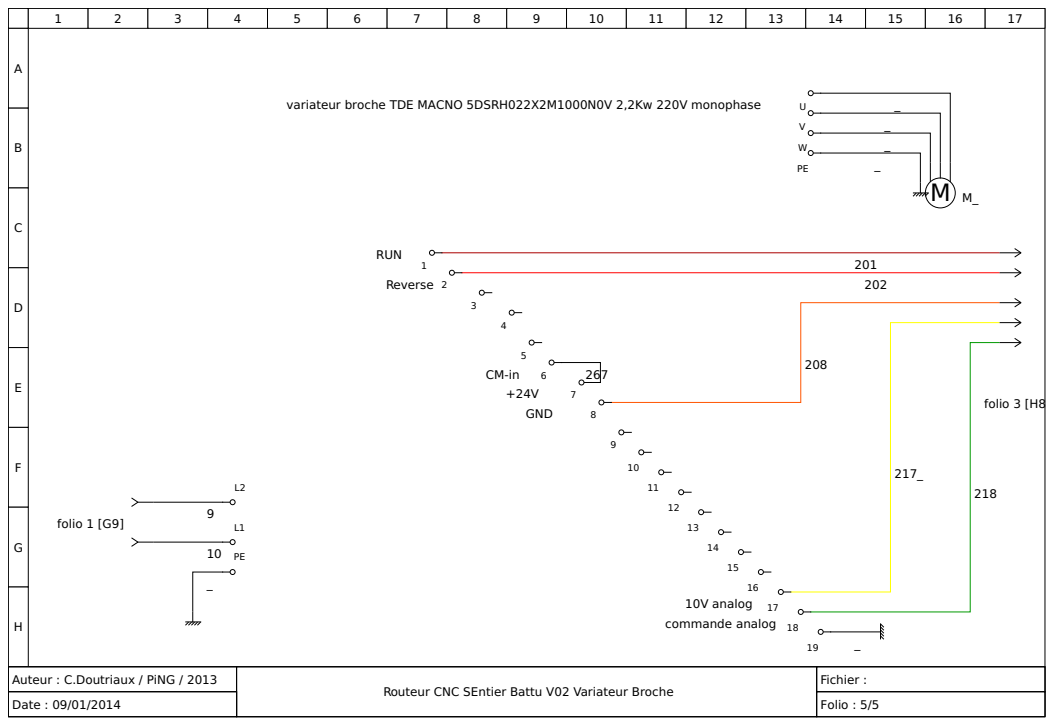
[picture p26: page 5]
Fichier :; folio 1 [G9]; folio 3 [H8; GND; RUN; 10V analog commande analog; Reverse

variateur broche TDE MACNO 5DSRH022X2M1000N0V 2,2Kw 220V monophase

Auteur : C.Doutriaux / PiNG / 2013

Routeur CNC SEntier Battu V02 Variateur Broche

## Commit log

2015-04-08 add all files
    [Liste des composants.xls, SmootieBox.scad, SmootieBox.stl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]
2015-04-08 clean directories
    [bom.sentierBattu.ods, budget_2_CNC.ods]
